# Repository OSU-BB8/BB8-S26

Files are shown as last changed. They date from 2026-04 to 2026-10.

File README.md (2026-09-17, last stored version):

# Picar-X

Picar-X Python library for Raspberry Pi.

## Links

- Docs: <https://docs.sunfounder.com/projects/picar-x-v20/en/latest/>
- Robot Hat: <https://docs.sunfounder.com/projects/robot-hat-v4/en/latest/>
- Forum: <https://forum.sunfounder.com/>
- Sunfounder: <https://www.sunfounder.com/>

## Installation

 > **Note**
  You also need to install robot_hat, vilib, sunfounder_controller and other dependent libraries.\
  <https://docs.sunfounder.com/projects/picar-x-v20/en/latest/python/python_start/install_all_modules.html>

```bash
# Install robot_hat
git clone --depth 1 -b 2.5.x https://github.com/sunfounder/robot-hat.git
cd robot-hat
sudo python3 install.py

# Install vilib
git clone --depth 1 https://github.com/sunfounder/vilib.git
cd vilib
sudo python3 install.py

# Install picar-x
git clone -b 2.1.x https://github.com/sunfounder/picar-x.git
cd picar-x
sudo pip3 install . --break
```

## Debug

Debug command records

```bash
cd ~/picar-x && sudo pip3 install . --break --no-deps --no-build-isolation
```

## Debug records

```bash
sudo pip3 uninstall picar-x --break -y && cd ~/picar-x && sudo pip3 install . --break --no-deps --no-build-isolation
sudo pip3 uninstall robot_hat --break -y && cd ~/robot-hat && sudo pip3 install . --break --no-deps --no-build-isolation
sudo python3 ~/picar-x/examples/14_voice_active_car_gpt.py
```

----------------------------------------------

## About SunFounder

SunFounder is a technology company focused on Raspberry Pi and Arduino open source community development. Committed to the promotion of open source culture, we strives to bring the fun of electronics making to people all around the world and enable everyone to be a maker. Our products include learning kits, development boards, robots, sensor modules and development tools. In addition to high quality products, SunFounder also offers video tutorials to help you make your own project. If you have interest in open source or making something cool, welcome to join us!

----------------------------------------------

## License

This program is free software; you can redistribute it and/or modify it under the terms of the GNU General Public License as published by the Free Software Foundation; either version 2 of the License, or (at your option) any later version.

This program is distributed in the hope that it will be useful, but WITHOUT ANY WARRANTY; without even the implied wa rranty of MERCHANTABILITY or FITNESS FOR A PARTICULAR PURPOSE. See the GNU General Public License for more details.

You should have received a copy of the GNU General Public License along with this program; if not, write to the Free Software Foundation, Inc., 51 Franklin Street, Fifth Floor, Boston, MA 02110-1301 USA.

{Repository Name} comes with ABSOLUTELY NO WARRANTY; for details run ./show w. This is free software, and you are welcome to redistribute it under certain conditions; run ./show c for details.

SunFounder, Inc., hereby disclaims all copyright interest in the program '{Repository Name}' (which makes passes at compilers).

Mike Huang, 21 August 2015

Mike Huang, Chief Executive Officer

Email: service@sunfounder.com, support@sunfounder.com

----------------------------------------------

## Contact us

website:
    www.sunfounder.com

E-mail:
    service@sunfounder.com, support@sunfounder.com

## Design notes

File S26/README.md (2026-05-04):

# BB8-S26
Welcome to the BB8 project! This repo has all the files that we used to develop the BB8 as well as a ton of old files from previous groups.

To test out the project, a few things need to be done first.

1. Plug the Pi on the main BB8 (Not the test one in the chassis) to a power source
2. You will need to connect the Pi to a monitor to find out its IP address and connect it to eduroam or whichever network you want to use.
3. The robot has two modes right now: The PS5 controller mode and the head-body communication mode that reads april tags.

PS5 Controller Mode:
1. Pair the PS5 controller with the body Pi (The one in the sphere). You can do this from the terminal or GUI
2. Plug in the 24V LiPo battery to the robot. This connects to everything except the Pi (which is a Pi 4B - definitely could use the upgrade to a 5, which should be in the materials).
3. Plug in the 3.7V with boost converter into the Pi and disconnect anything external from it.
4. Connect the shell so that it encapsulates the entire robot.
5. SSH into the body Pi. The user is "bb8" and password is "password" (I know right).
6. Navigate to /'BB8 Files'/'Body Files' 
7. Run the python files "PS5_Controller.py"
8. This will give you a menu of options to select. The two main ones are options 5 and 6. Choose 5 if you want the option that will balance the head and balance the body (Although the pendulum body balancer doesn't work well since the PID values are 0 for now). Option 6 gives the user full control over all the motors and functions.

Head-Body Communication:
1.You'll want to power up the head's Pi. This can be found on the picar, which we used for testing and then placed inside the head for Demo purposes.
2. Plug in the Head's Pi and navigate to the terminal. Form here, you should look at the terminal and find out the IP address.
3. Instead of pairing the PS5 Controller, go to the file "Expo_Demo.py" in 'BB8 Files'/'Expo Demo'. Replace the IP address in it with the new body IP address.
4. Make sure both the Body and the Head Pi's are turned on. 
5. Run Body_communication.py ON THE BODY. This opens up a UDP socket and waits for commands from the head.
6. Run Head_Communication.py ON THE HEAD. This allows you to send commands from the head to the body.
7. If you want to SSH into the head Pi, the user is "bb8camera" and the password is "password".

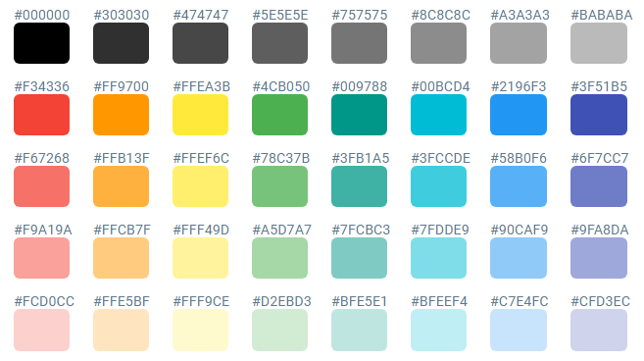
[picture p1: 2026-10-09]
F26/Head Code/April_Tag/docs/assets/media/colorboard_palette.png

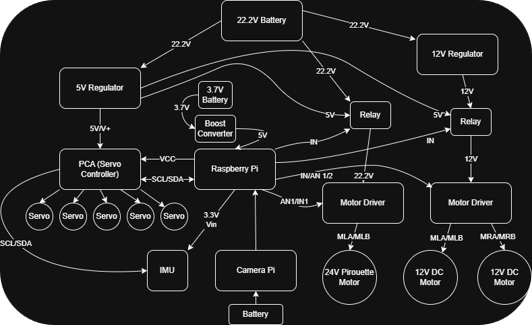
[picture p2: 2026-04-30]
S26/Electrical Flowchart.png

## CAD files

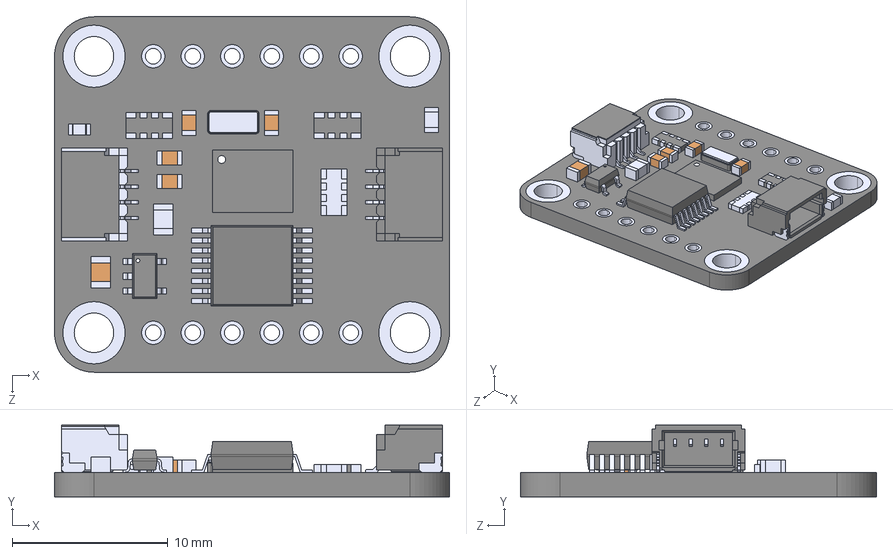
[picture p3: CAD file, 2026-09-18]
F26/PCB/Symbols & Footprints/BNO085/BNO085.step
25.4 x 4.60 x 22.9 mm
SPX5205M5
MAX4661CAE+

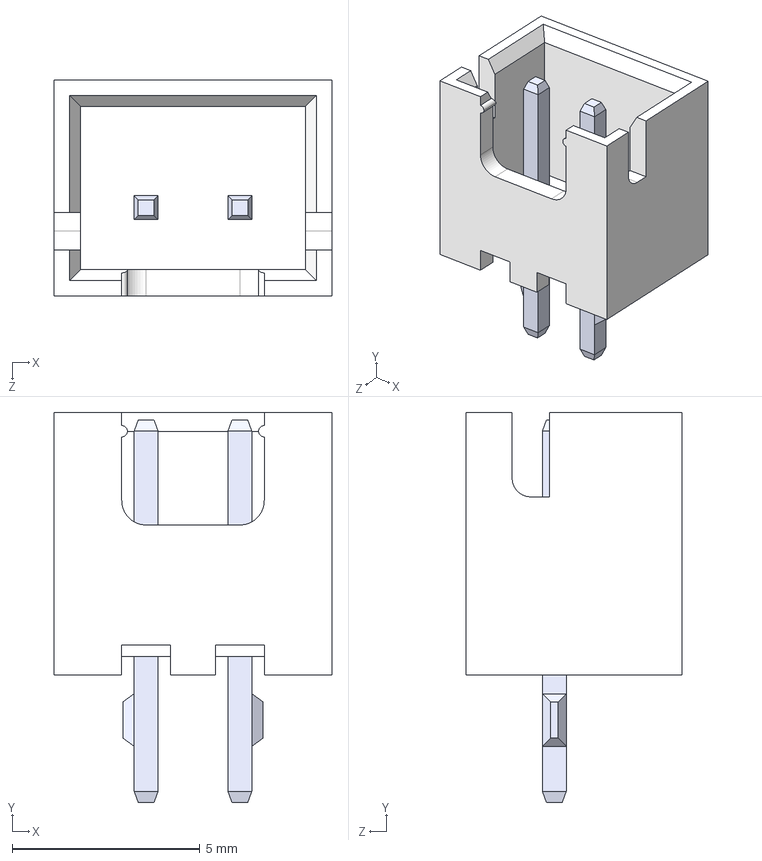
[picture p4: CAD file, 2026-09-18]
F26/PCB/Symbols & Footprints/JST/JST.step
7.40 x 10.4 x 5.75 mm

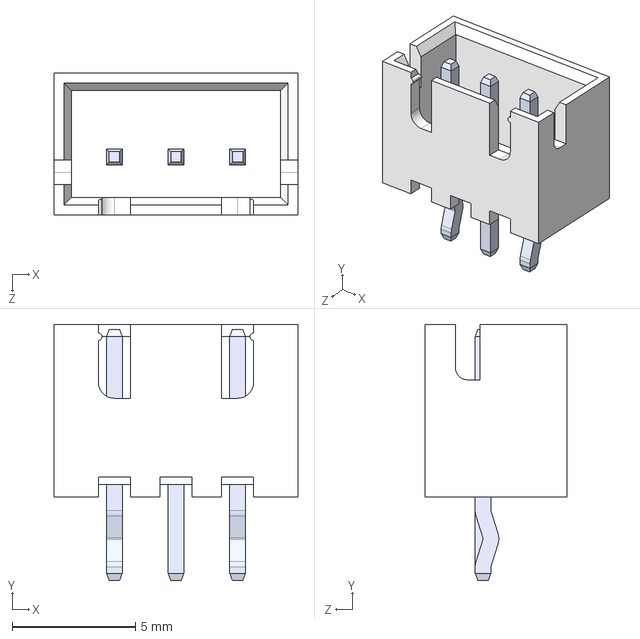
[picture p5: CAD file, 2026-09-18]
F26/PCB/Symbols & Footprints/JST3/JST3.step
9.90 x 10.4 x 5.75 mm

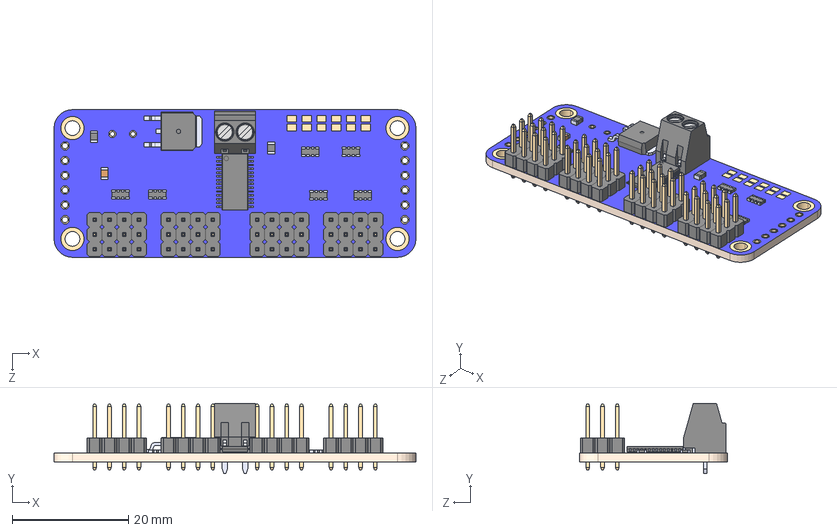
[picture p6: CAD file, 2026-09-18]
F26/PCB/Symbols & Footprints/PCA9685/PCA9685.step
62.2 x 12.1 x 25.4 mm
AOD417
TERMBLOCK_1X2-3.5MM
PCA9685_PCA9685
RESPACK_4X0603_220_ x 6

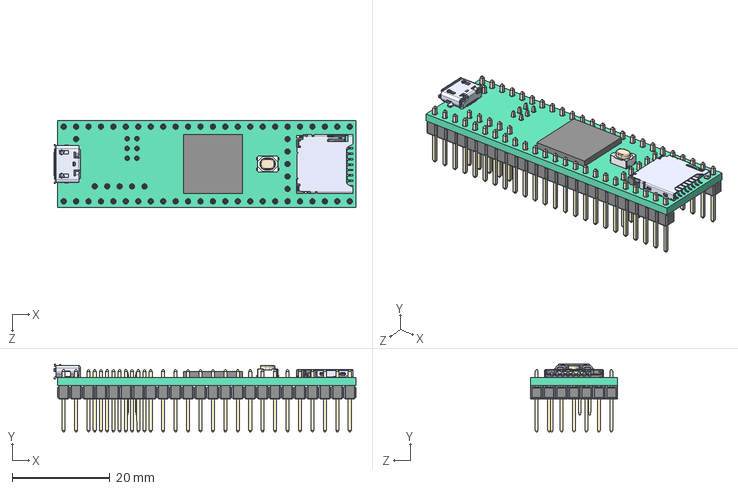
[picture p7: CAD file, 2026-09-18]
F26/PCB/Symbols & Footprints/Teensy/Teensy.step
61.7 x 13.8 x 17.8 mm

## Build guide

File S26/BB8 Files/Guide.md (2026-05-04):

Guide to the Files in this Directory:

1. Archive: Contains all the old, obsolete code for the project. Some are python files we developed, and others are C files for the Arduino from further back.

2. Body Files: Contains all the files to be used by the Body Pi.

3. Camera Files: Contains all the files to be used by the Head Pi.

4. Demo Videos: Contains videos that we got from demonstrations.

5. Expo Demo: Contains code that was used by the Head Pi for demonstrations.

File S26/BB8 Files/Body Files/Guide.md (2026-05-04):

Guide to the Files in this Directory:

1. Body_Communication: This is the file that receives commands from the head. If you want to run any APRILTag stuff, run the Body_Communication file on the Body Pi first.

2. Dead_Reckoning: This file allows the robot to locate how far it traveled from where it started. Currently, it doesn't work very well and isn't integrated into the system as a result. 

3. IMU: This file read the IMU data and sends it off the the Body via I2C.

4. Movement_Functions: This file contains all the movement functions and maps them to various motors or servos. If you want to control the robot, you must use a function from this file.

5. PID: This function has a basic PID class in it. The Movement_Functions uses it in its update_balance function.

6. PS5_Controller: This file allows a user to control the BB8 using a PS5 controller. To use it, simply make sure the Pi reads and is paired to your PS5 controller and run this code. When prompted, selected either option 5 or 6.

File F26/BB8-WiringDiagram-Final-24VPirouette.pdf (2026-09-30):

Vin 3Vo GND SDA SCL RST PS0 PS1 INT ADRBNO055 IMU

# PCA9685 GNDOE SCL SDA VCCV+ GND OESCL SDA VCC V+

## SmartDriveDuo-30

MLB
MLA
VB-VB+
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
AN2 ⁰ ¹ ² ³ ⁴ ⁵ ⁶ ⁷ ⁸ ⁹ ¹⁰ ¹¹ ¹² ¹³ ¹⁴ ¹⁵ PWM V+ GND 3V3 GPIO ² GPIO ³ GPIO ⁴ GND GPIO ¹⁷ GPIO ²⁷ GPIO ²² 3v3 GPIO ¹⁰ GPIO ⁹ GPIO ¹¹ GND GPIO ⁰ GPIO ⁵ GPIO ⁶ GPIO ¹³ GPIO ¹⁹ GPIO ²⁶ GND ⁵V5V GND GPIO ¹⁴ GPIO ¹⁵ GPIO ¹⁸ GND GPIO ²³ GPIO ²⁴ GND GPIO ²⁵ GPIO ⁸ GPIO ⁷ GPIO ¹ GND GPIO ¹² GND GPIO ¹⁶ GPIO ²⁰ GPIO ²¹ Raspberry Pi

4-Wire Connector
(Make Sure to line up)

## SmartDriveDuo-30

MLB
MLA
VB-VB+
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
4-Wire Connector
(Make Sure to line up)

## Drive Motor (Left)

## 22.2V LiPo Battery

2-Wire Connection
(Auto Lines up)

1 2 3 4 5 6

## Chunzehui F-1011

## Castle CC-BEC Pro

(5V)

Circle Thingy
(Wires Wrapped Around)

## Drive Motor (Right)

Red

Black | 2 Red

# 2 Black 1 Red ⁽Power) 1 Black ⁽GND⁾

## Swing Pendulum Servo (Front)

White Wire

Red Wire

Black Wire

## Swing Pendulum Servo (Back)

### 3 Wires

Basically
Together

Head Servo
(Move Left & Right)

Head Servo
(Move Forward
& Backward)

Head
Spinning
Servo

Yellow
Brown

Red

12V
Pirouette Motor
(Bottom)

## Castle CC-BEC Pro

(12V) Circle Thingy
(Wires
Wrapped
Around)

V+

GND

GND Wire

## 5V Signal Relay

(12V)

IN
GND
PWR

NC
NO
COM

## 5V Signal Relay

(24V)

IN
GND
PWR

NC
NO
COM

--- C:\Users\sawhu\OneDrive - Oklahoma A and M System\Documents\LTspice\BB8 - Final Wiring Diagram (24V Motor).asc ---

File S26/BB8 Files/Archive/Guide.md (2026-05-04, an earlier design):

Guide to the Files in this directory:

1. Body/Old Code: Contains Arduino code that old groups used.

2. Continuous Spin Tests: Old code to test the motors. Probably not working anymore due to the changes we made.

3. Dome: Old Arduino code for the head system.

4. Remote: Old code to control BB8 using a phone.

5. Scampa123s BB8 Code: More old code written for Arduino.

6. Test Files: Old files that we developed in Python. Might be worth looking at if needing some ideas or wanting to figure out how system works.

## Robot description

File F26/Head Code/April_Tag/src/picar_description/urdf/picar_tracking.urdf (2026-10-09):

<?xml version="1.0"?>
<!--
  picar_tracking.urdf  (V3)
  URDF for live RViz visualization.  Root frame is 'car_base', published by
  tf_bridge as 'world -> car_base'.  Pan and tilt are revolute joints; their
  positions come from /joint_states published by tf_bridge each frame.

  Coordinate convention (all frames, including car_base):
    +X = image right
    +Y = image down  (OpenCV / pupil-apriltags camera convention)
    +Z = optical axis (forward, toward tags)

  Physical kinematic chain (parent -> child):
    car_base (chassis level)
      -> pan_joint  (revolute, Y-axis, yaw / pan)    height ~6 cm above chassis
      -> tilt_joint (revolute, X-axis, pitch / tilt)  height ~2 cm above pan
      -> camera     (fixed, camera optical frame)      height ~1.5 cm above tilt

  Joint offsets are approximate.  Each is marked with TUNE and should be
  verified against physical measurements and/or compared with RViz after a
  live-pan test (car_base world position should remain stable as servos move).
-->
<robot name="picar_tracking">

  <material name="picar_white">
    <color rgba="0.9 0.9 0.9 1.0"/>
  </material>
  <material name="picar_black">
    <color rgba="0.1 0.1 0.1 1.0"/>
  </material>
  <material name="picar_gray">
    <color rgba="0.5 0.5 0.5 1.0"/>
  </material>
  <material name="picar_blue">
    <color rgba="0.2 0.4 0.85 0.85"/>
  </material>

  <!-- ROOT: car body frame — published by tf_bridge as 'world -> car_base'. -->
  <!-- No visual here; chassis box is a separate child link.                 -->
  <link name="car_base"/>

  <!-- Pan servo link — visualised as a small horizontal cylinder -->
  <link name="pan_link">
    <visual>
      <origin xyz="0 0 0" rpy="1.5708 0 0"/>
      <geometry>
        <cylinder length="0.05" radius="0.008"/>
      </geometry>
      <material name="picar_gray"/>
    </visual>
  </link>
  <!--
    TUNE: pan servo is approximately 6 cm above car_base (-Y = up in camera
    convention).  Adjust xyz y-value after visual inspection in RViz.
  -->
  <joint name="pan_joint" type="revolute">
    <parent link="car_base"/>
    <child link="pan_link"/>
    <origin xyz="0.0 -0.060 0.0" rpy="0 0 0"/>
    <axis xyz="0 1 0"/>
    <limit lower="-1.5708" upper="1.5708" effort="1.0" velocity="1.0"/>
  </joint>

  <!-- Tilt servo link — visualised as a small vertical cylinder -->
  <link name="tilt_link">
    <visual>
      <origin xyz="0 0 0" rpy="0 0 0"/>
      <geometry>
        <cylinder length="0.03" radius="0.008"/>
      </geometry>
      <material name="picar_gray"/>
    </visual>
  </link>
  <!-- TUNE: tilt servo is approximately 2 cm above pan_link. -->
  <joint name="tilt_joint" type="revolute">
    <parent link="pan_link"/>
    <child link="tilt_link"/>
    <origin xyz="0.0 -0.020 0.0" rpy="0 0 0"/>
    <axis xyz="1 0 0"/>
    <limit lower="-0.6109" upper="0.6109" effort="1.0" velocity="1.0"/>
  </joint>

  <!-- Camera optical frame — matches tf_bridge 'camera' TF convention.      -->
  <!-- Small blue box at the camera lens position.                            -->
  <link name="camera">
    <visual>
      <origin xyz="0 0 0" rpy="0 0 0"/>
      <geometry>
        <box size="0.025 0.025 0.02"/>
      </geometry>
      <material name="picar_blue"/>
    </visual>
  </link>
  <!-- TUNE: camera lens is approximately 1.5 cm above tilt_link. -->
  <joint name="camera_optical_joint" type="fixed">
    <parent link="tilt_link"/>
    <child link="camera"/>
    <origin xyz="0.0 -0.015 0.0" rpy="0 0 0"/>
  </joint>

  <!-- Camera pan/tilt mount column — purely visual, child of camera. -->
  <link name="camera_mount">
    <visual>
      <origin xyz="0 0 0" rpy="0 0 0"/>
      <geometry>
        <box size="0.03 0.07 0.03"/>
      </geometry>
      <material name="picar_gray"/>
    </visual>
  </link>
  <joint name="camera_to_mount" type="fixed">
    <parent link="camera"/>
    <child link="camera_mount"/>
    <!-- column is below (+Y=down) and slightly behind (-Z) the camera lens -->
    <origin xyz="0.0 0.045 -0.01" rpy="0 0 0"/>
  </joint>

  <!-- Car chassis — 14 cm wide, 4 cm tall, 20 cm long (camera convention). -->
  <link name="base_link">
    <visual>
      <origin xyz="0 0 0" rpy="0 0 0"/>
      <geometry>
        <box size="0.14 0.04 0.20"/>
      </geometry>
      <material name="picar_white"/>
    </visual>
  </link>
  <!--
    TUNE: chassis centre is 5 cm behind car_base along the optical axis (-Z
    offset).  The Y offset keeps chassis box at approximately car_base height
    (no vertical offset since car_base is defined at chassis-top level).
    Adjust after visual inspection in RViz.
  -->
  <joint name="car_base_to_chassis" type="fixed">
    <parent link="car_base"/>
    <child link="base_link"/>
    <origin xyz="0.0 0.0 -0.05" rpy="0 0 0"/>
  </joint>

  <!-- Front left wheel -->
  <link name="front_left_wheel">
    <visual>
      <origin xyz="0 0 0" rpy="0 1.5708 0"/>
      <geometry>
        <cylinder length="0.03" radius="0.033"/>
      </geometry>
      <material name="picar_black"/>
    </visual>
  </link>
  <joint name="chassis_to_fl_wheel" type="fixed">
    <parent link="base_link"/>
    <child link="front_left_wheel"/>
    <origin xyz="-0.07 0.02 0.07" rpy="0 0 0"/>
  </joint>

  <!-- Front right wheel -->
  <link name="front_right_wheel">
    <visual>
      <origin xyz="0 0 0" rpy="0 1.5708 0"/>
      <geometry>
        <cylinder length="0.03" radius="0.033"/>
      </geometry>
      <material name="picar_black"/>
    </visual>
  </link>
  <joint name="chassis_to_fr_wheel" type="fixed">
    <parent link="base_link"/>
    <child link="front_right_wheel"/>
    <origin xyz="0.07 0.02 0.07" rpy="0 0 0"/>
  </joint>

  <!-- Rear left wheel -->
  <link name="rear_left_wheel">
    <visual>
      <origin xyz="0 0 0" rpy="0 1.5708 0"/>
      <geometry>
        <cylinder length="0.03" radius="0.033"/>
      </geometry>
      <material name="picar_black"/>
    </visual>
  </link>
  <joint name="chassis_to_rl_wheel" type="fixed">
    <parent link="base_link"/>
    <child link="rear_left_wheel"/>
    <origin xyz="-0.07 0.02 -0.07" rpy="0 0 0"/>
  </joint>

  <!-- Rear right wheel -->
  <link name="rear_right_wheel">
    <visual>
      <origin xyz="0 0 0" rpy="0 1.5708 0"/>
      <geometry>
        <cylinder length="0.03" radius="0.033"/>
      </geometry>
      <material name="picar_black"/>
    </visual>
  </link>
  <joint name="chassis_to_rr_wheel" type="fixed">
    <parent link="base_link"/>
    <child link="rear_right_wheel"/>
    <origin xyz="0.07 0.02 -0.07" rpy="0 0 0"/>
  </joint>

</robot>

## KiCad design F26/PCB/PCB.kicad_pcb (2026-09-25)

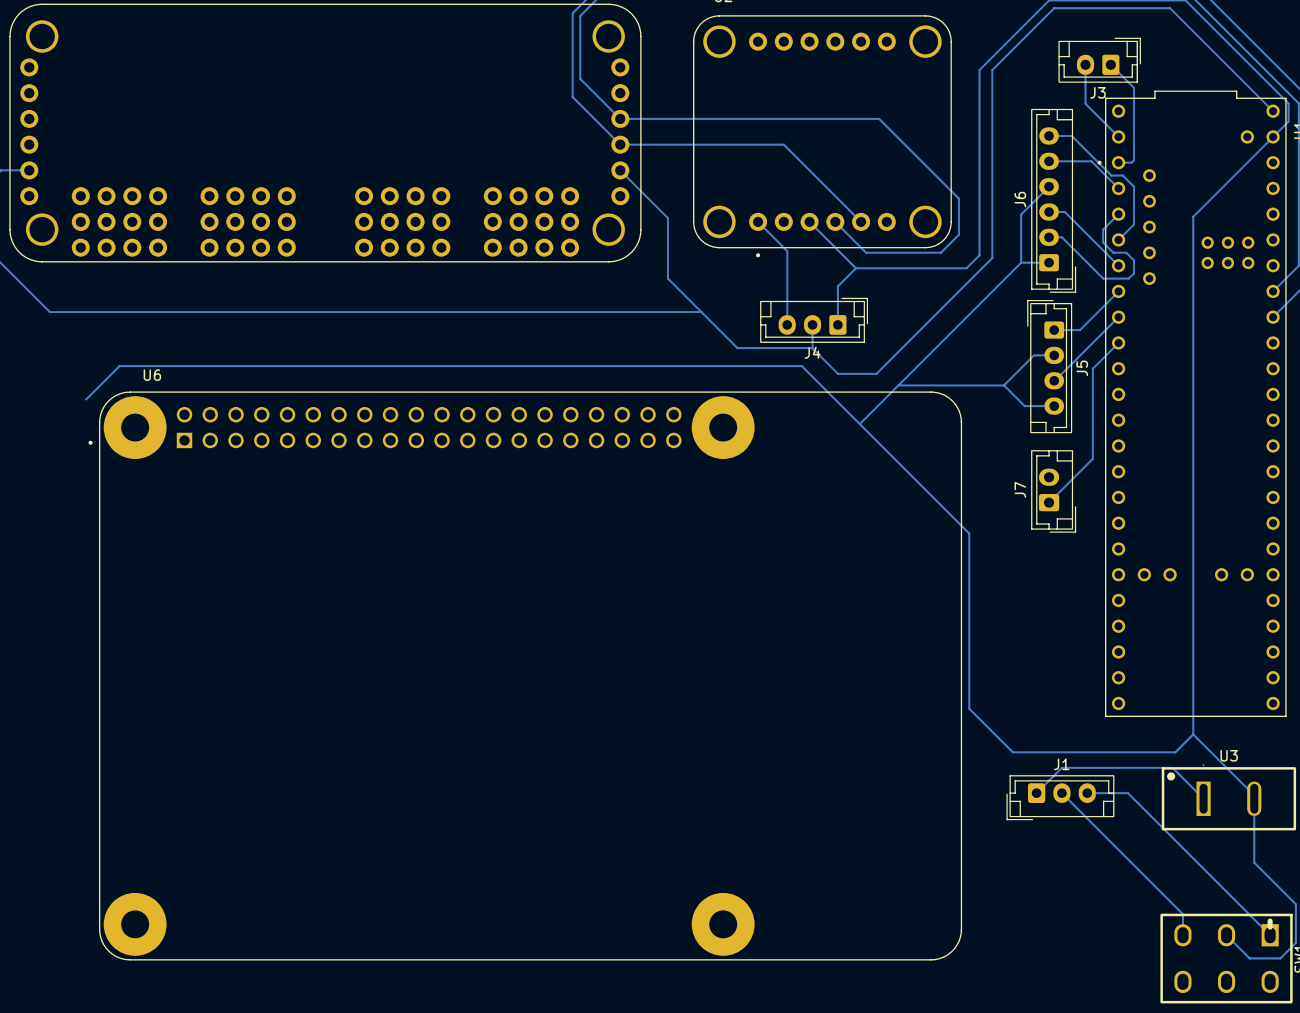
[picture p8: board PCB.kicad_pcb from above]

Board: 2 copper layers, 12 parts (0 on the bottom side), 23 nets.

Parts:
J1, J4: B3B-XH-A; JST_EH_B3B-EH-A_1x03_P2.50mm_Vertical
J3: B2B-XH-A; JST_EH_B2B-EH-A_1x02_P2.50mm_Vertical
J5: Conn_01x04; JST_EH_B4B-EH-A_1x04_P2.50mm_Vertical
J6: Conn_01x06; JST_EH_B6B-EH-A_1x06_P2.50mm_Vertical
J7: Conn_01x02; JST_EH_B2B-EH-A_1x02_P2.50mm_Vertical
SW1: SW_Nidec_CAS-120A1; Mini_Toggle_DPDT_4.3x4.6mm
U1: Teensy
U2: MODULE_BNO085
U3: Switch_2Pin_5mm_ParallelBlades
U4: 815; MODULE_PCA9685
U6: SC0194_9_; MODULE_SC0194_9_

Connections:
3V3: U6.1 (3V3), U6.17 (3V3)
5V0: U6.2 (5V0), U6.4 (5V0)
GND: U4.GND_1 (GND), U4.GND_2 (GND), U4.GND_3 (GND), U4.GND_4 (GND), U4.GND_5 (GND), U4.GND_6 (GND), U4.GND_7 (GND), U4.GND_8 (GND), U4.GND_9 (GND), U4.GND_10 (GND), U4.GND_11 (GND), U4.GND_12 (GND), U4.GND_13 (GND), U4.GND_14 (GND), U4.GND_15 (GND), U4.GND_16 (GND), U4.GND_17 (GND), U4.GND_18 (GND), U6.6 (GND), U6.9 (GND), U6.14 (GND), U6.20 (GND), U6.25 (GND), U6.30 (GND), U6.34 (GND), U6.39 (GND)
unnamed: J1.1, U3.1
unnamed: J5.1, U1.6 (OUT1D)
unnamed: J4.1, J5.2, J5.4, J6.1, J6.4, SW1.2 (B), U1.GND, U2.3 (GND), U3.2
unnamed: J5.3, U1.7 (OUT1A)
unnamed: J6.2, U1.3 (LRCLK2)
unnamed: J6.3, U1.5 (IN2)
unnamed: J6.5, U1.2 (OUT2)
unnamed: J6.6, U1.4 (BCLK2)
unnamed: J7.1 (Pin_1_1), U1.8 (IN1)
unnamed: J1.2, SW1.3 (A)
unnamed: J1.3, SW1.1 (C)
unnamed: U1.18 (A4), U2.5 (SDA), U4.SDA_1 (SDA), U4.SDA_2 (SDA)
unnamed: U1.19 (A5), U2.4 (SCL), U4.SCL_1 (SCL), U4.SCL_2 (SCL)
unnamed: J3.2, U1.0 (RX1)
unnamed: J3.1, U1.1 (TX1)
unnamed: J4.3, U2.1 (VIN)
unnamed: U4.OE_1 (~OE), U4.OE_2 (~OE)
SHIELD: U6.S1 (SHIELD), U6.S2 (SHIELD), U6.S3 (SHIELD), U6.S4 (SHIELD)
V+: U4.V+_1 (V+), U4.V+_2 (V+), U4.V+_3 (V+), U4.V+_4 (V+), U4.V+_5 (V+), U4.V+_6 (V+), U4.V+_7 (V+), U4.V+_8 (V+), U4.V+_9 (V+), U4.V+_10 (V+), U4.V+_11 (V+), U4.V+_12 (V+), U4.V+_13 (V+), U4.V+_14 (V+), U4.V+_15 (V+), U4.V+_16 (V+), U4.V+_17 (V+), U4.V+_18 (V+)
VCC: J4.2, U1.Vin, U4.VCC_1 (VCC), U4.VCC_2 (VCC)

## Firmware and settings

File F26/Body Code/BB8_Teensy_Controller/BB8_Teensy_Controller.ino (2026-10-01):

/*
  BB-8 Teensy 4.1 Motor / Navigation Controller

  Pi sends:
      T,<distance_ft>,<angle_deg>\n
  Example:
      T,15.7,-32.5

  Teensy replies periodically:
      S,<state>,<distance>,<angle>,<pitch>,<roll>,<drive>,<swing>,<pivot>

  IMPORTANT:
  - Verify all Teensy pin assignments below before connecting motor drivers.
  - Teensy 4.1 GPIO is 3.3 V logic.
  - Pi and Teensy MUST share GND.
  - Motor power must NOT come from the Teensy.
*/

#include <Arduino.h>
#include <Wire.h>
#include <Adafruit_PWMServoDriver.h>
#include <Adafruit_BNO08x.h>

// ============================================================
// PIN ASSIGNMENTS - CHANGE TO MATCH NEW WIRING
// ============================================================

// Pi UART: Teensy Serial1 RX=0, TX=1
constexpr uint8_t DRIVE1_PHASE_PIN  = 2;
constexpr uint8_t DRIVE1_PWM_PIN    = 3;
constexpr uint8_t DRIVE2_PHASE_PIN  = 4;
constexpr uint8_t DRIVE2_PWM_PIN    = 5;
constexpr uint8_t PIVOT_PHASE_PIN   = 6;
constexpr uint8_t PIVOT_PWM_PIN     = 7;

constexpr uint8_t RELAY1_PIN = 8;

// PCA9685
constexpr uint8_t PCA_ADDRESS = 0x40;
constexpr uint8_t SWING1_CH = 0;
constexpr uint8_t SWING2_CH = 4;

// Head servos (same PCA9685 channels as the original Pi controller)
constexpr uint8_t HEAD_FB_CH  = 1;  // head forward/back
constexpr uint8_t HEAD_STS_CH = 2;  // head side-to-side

// ============================================================
// CONFIGURATION
// ============================================================

constexpr uint32_t PI_BAUD = 115200;
constexpr uint32_t USB_BAUD = 115200;

constexpr float FOLLOW_START_DISTANCE_FT = 5.0f;
constexpr float FOLLOW_STOP_DISTANCE_FT  = 4.0f;
constexpr float HARD_MIN_DISTANCE_FT     = 3.0f;
constexpr float MAX_VALID_DISTANCE_FT    = 40.0f;

constexpr float MAX_DRIVE_SPEED = 0.30f;
constexpr float MIN_DRIVE_SPEED = 0.12f;
constexpr float FULL_SPEED_DISTANCE_FT = 18.0f;
constexpr float DRIVE_ACCEL_RATE = 0.40f;
constexpr float DRIVE_DECEL_RATE = 0.70f;

constexpr float ANGLE_DEADBAND_DEG = 6.0f;
constexpr float CLOSE_PIVOT_START_ANGLE_DEG = 30.0f;
constexpr float PIVOT_STOP_ANGLE_DEG = 10.0f;
constexpr float REAR_PIVOT_ANGLE_DEG = 65.0f;
constexpr float CLOSE_NAV_DISTANCE_FT = 10.0f;

constexpr float SWING_CENTER_DEG = 90.0f;
constexpr float MAX_SWING_OFFSET_DEG = 14.0f;
constexpr float SWING_KP = 0.35f;
constexpr float SWING_DIRECTION = 1.0f;
constexpr float MIN_SWING_OFFSET_DEG = 1.5f;
constexpr float SWING_SLEW_RATE_DEG_PER_SEC = 35.0f;

constexpr float PIVOT_KP = 0.022f;
constexpr float MIN_PIVOT_COMMAND = 0.10f;
constexpr float MAX_PIVOT_COMMAND = 0.25f;
constexpr float PIVOT_DIRECTION = -1.0f;

constexpr float DISTANCE_FILTER_ALPHA = 0.25f;
constexpr float ANGLE_FILTER_ALPHA = 0.30f;

constexpr uint32_t PI_TIMEOUT_MS = 500;
constexpr uint32_t CONTROL_PERIOD_US = 20000; // 50 Hz
constexpr uint32_t STATUS_PERIOD_MS = 250;

// Servo calibration.
// Tune these to your actual servos if necessary.
constexpr uint16_t SERVO_MIN_US = 500;
constexpr uint16_t SERVO_MAX_US = 2500;

// Head leveling configuration.
// Original Pi behavior was FB = 90 + pitch and STS = 90 + roll.
constexpr float HEAD_CENTER_DEG = 90.0f;
constexpr float HEAD_MIN_DEG = 55.0f;
constexpr float HEAD_MAX_DEG = 125.0f;
constexpr float HEAD_FB_OFFSET_DEG = 2.5f;
constexpr float HEAD_STS_OFFSET_DEG = -2.0f;
constexpr float HEAD_EMA_ALPHA = 0.15f;
constexpr float HEAD_PITCH_DIRECTION = 1.0f;
constexpr float HEAD_ROLL_DIRECTION  = 1.0f;

// ============================================================
// HARDWARE OBJECTS
// ============================================================

Adafruit_PWMServoDriver pca(PCA_ADDRESS);
Adafruit_BNO08x bno08x(-1);
sh2_SensorValue_t sensorValue;

bool imuOK = false;
float imuPitch = 0.0f;
float imuRoll = 0.0f;
float imuYaw = 0.0f;

// Smoothed head commands.
float headFBCommand = HEAD_CENTER_DEG;
float headSTSCommand = HEAD_CENTER_DEG;
bool headFilterInitialized = false;

// ============================================================
// CONTROLLER STATE
// ============================================================

enum NavState {
  STARTUP,
  WAITING_FOR_PI,
  IN_LEASH_ZONE,
  TARGET_REACHED,
  TOO_CLOSE,
  STRAIGHT,
  ARC,
  PIVOT,
  INVALID_TARGET,
  COMMS_LOST
};

NavState navState = STARTUP;

bool following = false;
bool pivoting = false;
bool systemEnabled = false;

bool haveFilteredTarget = false;
float filteredDistance = 0.0f;
float filteredAngle = 0.0f;

float currentDrive = 0.0f;
float currentSwing = SWING_CENTER_DEG;
float currentPivot = 0.0f;

uint32_t lastPacketMs = 0;
uint32_t lastControlUs = 0;
uint32_t lastStatusMs = 0;

char rxBuffer[80];
size_t rxIndex = 0;

// ============================================================
// HELPERS
// ============================================================

float clampf(float x, float lo, float hi) {
  if (x < lo) return lo;
  if (x > hi) return hi;
  return x;
}

float moveToward(float current, float target, float maxChange) {
  if (target > current) return min(current + maxChange, target);
  if (target < current) return max(current - maxChange, target);
  return current;
}

float normalizeAngle(float a) {
  while (a > 180.0f) a -= 360.0f;
  while (a < -180.0f) a += 360.0f;
  return a;
}

const char* stateName(NavState s) {
  switch (s) {
    case STARTUP: return "STARTUP";
    case WAITING_FOR_PI: return "WAIT_PI";
    case IN_LEASH_ZONE: return "LEASH";
    case TARGET_REACHED: return "REACHED";
    case TOO_CLOSE: return "TOO_CLOSE";
    case STRAIGHT: return "STRAIGHT";
    case ARC: return "ARC";
    case PIVOT: return "PIVOT";
    case INVALID_TARGET: return "INVALID";
    case COMMS_LOST: return "COMMS_LOST";
    default: return "UNKNOWN";
  }
}

// ============================================================
// MOTOR OUTPUT
// Phase/Enable behavior equivalent to gpiozero PhaseEnableMotor.
// ============================================================

void setPhaseEnableMotor(uint8_t phasePin, uint8_t pwmPin, float command) {
  command = clampf(command, -1.0f, 1.0f);

  if (fabsf(command) < 0.001f) {
    analogWrite(pwmPin, 0);
    digitalWrite(phasePin, LOW);
    return;
  }

  bool direction = command >= 0.0f;
  digitalWrite(phasePin, direction ? HIGH : LOW);

  int pwm = (int)roundf(fabsf(command) * 255.0f);
  pwm = constrain(pwm, 0, 255);
  analogWrite(pwmPin, pwm);
}

void drive(float command) {
  command = clampf(command, -MAX_DRIVE_SPEED, MAX_DRIVE_SPEED);
  setPhaseEnableMotor(DRIVE1_PHASE_PIN, DRIVE1_PWM_PIN, -command);
  setPhaseEnableMotor(DRIVE2_PHASE_PIN, DRIVE2_PWM_PIN, -command);
}

void steer(float command) {
  command = clampf(command, -1.0f, 1.0f);
  if (fabsf(command) < 0.01f) command = 0.0f;
  setPhaseEnableMotor(PIVOT_PHASE_PIN, PIVOT_PWM_PIN, command);
}

uint16_t servoPulseFromDegrees(float degrees) {
  degrees = clampf(degrees, 0.0f, 180.0f);
  float us = SERVO_MIN_US +
             (degrees / 180.0f) * (SERVO_MAX_US - SERVO_MIN_US);

  // PCA9685 at 50 Hz => 20,000 us period / 4096 counts.
  return (uint16_t)roundf(us * 4096.0f / 20000.0f);
}

void setServoDegrees(uint8_t channel, float degrees) {
  pca.setPWM(channel, 0, servoPulseFromDegrees(degrees));
}

void setHeadForwardBack(float degrees) {
  degrees = clampf(degrees, HEAD_MIN_DEG, HEAD_MAX_DEG);
  setServoDegrees(HEAD_FB_CH, degrees + HEAD_FB_OFFSET_DEG);
}

void setHeadSideToSide(float degrees) {
  degrees = clampf(degrees, HEAD_MIN_DEG, HEAD_MAX_DEG);
  setServoDegrees(HEAD_STS_CH, degrees + HEAD_STS_OFFSET_DEG);
}

void centerHead() {
  headFBCommand = HEAD_CENTER_DEG;
  headSTSCommand = HEAD_CENTER_DEG;
  headFilterInitialized = false;
  setHeadForwardBack(HEAD_CENTER_DEG);
  setHeadSideToSide(HEAD_CENTER_DEG);
}

void updateHeadLeveling() {
  if (!imuOK) return;

  // Match the original Raspberry Pi behavior:
  // forward/back follows pitch; side-to-side follows roll.
  float targetFB = HEAD_CENTER_DEG + HEAD_PITCH_DIRECTION * imuPitch;
  float targetSTS = HEAD_CENTER_DEG + HEAD_ROLL_DIRECTION * imuRoll;

  targetFB = clampf(targetFB, HEAD_MIN_DEG, HEAD_MAX_DEG);
  targetSTS = clampf(targetSTS, HEAD_MIN_DEG, HEAD_MAX_DEG);

  if (!headFilterInitialized) {
    headFBCommand = targetFB;
    headSTSCommand = targetSTS;
    headFilterInitialized = true;
  } else {
    headFBCommand += HEAD_EMA_ALPHA * (targetFB - headFBCommand);
    headSTSCommand += HEAD_EMA_ALPHA * (targetSTS - headSTSCommand);
  }

  setHeadForwardBack(headFBCommand);
  setHeadSideToSide(headSTSCommand);
}

void setSwing(float degrees) {
  // Preserve original Movement_Functions behavior:
  // difference = current_swing - 90 + swing_offset
  // servo1 = 90 + difference
  // servo2 = 90 - difference
  constexpr float swingOffset = -1.0f;

  degrees = clampf(degrees, 70.0f, 117.0f);
  float difference = degrees - 90.0f + swingOffset;

  setServoDegrees(SWING1_CH, 90.0f + difference);
  setServoDegrees(SWING2_CH, 90.0f - difference);
}

void enableSystem() {
  // Outputs are already zero before relays close.
  drive(0.0f);
  steer(0.0f);
  setSwing(90.0f);
  delay(20);

  digitalWrite(RELAY1_PIN, HIGH);
  systemEnabled = true;
}

void disableSystem() {
  drive(0.0f);
  steer(0.0f);
  setSwing(90.0f);

  digitalWrite(RELAY1_PIN, LOW);
  systemEnabled = false;
}

void emergencyStop(NavState reason) {
  currentDrive = 0.0f;
  currentPivot = 0.0f;
  currentSwing = SWING_CENTER_DEG;

  drive(0.0f);
  steer(0.0f);
  setSwing(SWING_CENTER_DEG);

  following = false;
  pivoting = false;
  navState = reason;
}

// ============================================================
// BNO085
// ============================================================

void setReports() {
  if (!imuOK) return;

  if (!bno08x.enableReport(SH2_ROTATION_VECTOR, 10000)) {
    Serial.println("WARNING: Could not enable BNO085 rotation vector");
  }
}

void quaternionToEuler(float qr, float qi, float qj, float qk,
                       float &yaw, float &pitch, float &roll) {
  float sqr = qr * qr;
  float sqi = qi * qi;
  float sqj = qj * qj;
  float sqk = qk * qk;

  yaw = atan2f(2.0f * (qi * qj + qk * qr),
               (sqi - sqj - sqk + sqr));

  float sinp = -2.0f * (qi * qk - qj * qr);
  sinp = clampf(sinp, -1.0f, 1.0f);
  pitch = asinf(sinp);

  roll = atan2f(2.0f * (qj * qk + qi * qr),
                (-sqi - sqj + sqk + sqr));

  constexpr float RAD_TO_DEG_F = 57.2957795f;
  yaw *= RAD_TO_DEG_F;
  pitch *= RAD_TO_DEG_F;
  roll *= RAD_TO_DEG_F;
}

void updateIMU() {
  if (!imuOK) return;

  if (bno08x.wasReset()) {
    setReports();
  }

  while (bno08x.getSensorEvent(&sensorValue)) {
    if (sensorValue.sensorId == SH2_ROTATION_VECTOR) {
      quaternionToEuler(
        sensorValue.un.rotationVector.real,
        sensorValue.un.rotationVector.i,
        sensorValue.un.rotationVector.j,
        sensorValue.un.rotationVector.k,
        imuYaw, imuPitch, imuRoll
      );
    }
  }
}

// ============================================================
// TARGET FILTER
// ============================================================

void resetTargetFilter() {
  haveFilteredTarget = false;
}

void filterTarget(float distance, float angle) {
  angle = normalizeAngle(angle);

  if (!haveFilteredTarget) {
    filteredDistance = distance;
    filteredAngle = angle;
    haveFilteredTarget = true;
    return;
  }

  filteredDistance =
      DISTANCE_FILTER_ALPHA * distance +
      (1.0f - DISTANCE_FILTER_ALPHA) * filteredDistance;

  float error = normalizeAngle(angle - filteredAngle);

  filteredAngle = normalizeAngle(
      filteredAngle + ANGLE_FILTER_ALPHA * error
  );
}

// ============================================================
// PI SERIAL PROTOCOL
// ============================================================

void handleCommand(char *line) {
  // Target packet: T,distance_ft,angle_deg
  if (line[0] == 'T' && line[1] == ',') {
    char *p1 = strchr(line + 2, ',');
    if (!p1) return;

    *p1 = '\0';

    float distance = atof(line + 2);
    float angle = atof(p1 + 1);

    if (!isfinite(distance) || !isfinite(angle) ||
        distance < 0.0f || distance > MAX_VALID_DISTANCE_FT) {
      emergencyStop(INVALID_TARGET);
      return;
    }

    filterTarget(distance, angle);
    lastPacketMs = millis();

    // Do not energize motor power until first valid command.
    if (!systemEnabled) enableSystem();

    return;
  }

  // Pause movement but KEEP motor power / relays enabled.
  if (strcmp(line, "PAUSE") == 0) {
      emergencyStop(WAITING_FOR_PI);

      // Throw away the old target so BB-8 cannot resume
      // toward stale beacon data.
      resetTargetFilter();

      // Keep the system enabled.
      // DO NOT call disableSystem().
      if (!systemEnabled) {
          enableSystem();
      }

      // PAUSE counts as valid Pi communication.
      lastPacketMs = millis();

      return;
  }

  // Explicit stop from Pi.
  if (strcmp(line, "STOP") == 0) {
    emergencyStop(WAITING_FOR_PI);
    disableSystem();
    resetTargetFilter();
    return;
  }

  // Optional heartbeat that does NOT command motion.
  if (strcmp(line, "PING") == 0) {
    Serial1.println("PONG");
    return;
  }
}

void readPiSerial() {
  while (Serial1.available()) {
    char c = (char)Serial1.read();

    if (c == '\r') continue;

    if (c == '\n') {
      rxBuffer[rxIndex] = '\0';
      if (rxIndex > 0) handleCommand(rxBuffer);
      rxIndex = 0;
      continue;
    }

    if (rxIndex < sizeof(rxBuffer) - 1) {
      rxBuffer[rxIndex++] = c;
    } else {
      // Overflow = discard packet safely.
      rxIndex = 0;
    }
  }
}

// ============================================================
// NAVIGATION
// ============================================================

float calculateDriveSpeed(float distance) {
  if (distance <= FOLLOW_STOP_DISTANCE_FT) return 0.0f;
  if (distance >= FULL_SPEED_DISTANCE_FT) return MAX_DRIVE_SPEED;

  float progress =
      (distance - FOLLOW_STOP_DISTANCE_FT) /
      (FULL_SPEED_DISTANCE_FT - FOLLOW_STOP_DISTANCE_FT);

  float speed =
      MIN_DRIVE_SPEED +
      progress * (MAX_DRIVE_SPEED - MIN_DRIVE_SPEED);

  return clampf(speed, MIN_DRIVE_SPEED, MAX_DRIVE_SPEED);
}

float calculateSwingTarget(float angle) {
  if (fabsf(angle) <= ANGLE_DEADBAND_DEG)
    return SWING_CENTER_DEG;

  float offset = angle * SWING_KP * SWING_DIRECTION;
  offset = clampf(offset, -MAX_SWING_OFFSET_DEG,
                  MAX_SWING_OFFSET_DEG);

  if (fabsf(offset) > 0.0f &&
      fabsf(offset) < MIN_SWING_OFFSET_DEG) {
    offset = copysignf(MIN_SWING_OFFSET_DEG, offset);
  }

  return SWING_CENTER_DEG + offset;
}

float calculatePivotCommand(float angle) {
  if (fabsf(angle) <= PIVOT_STOP_ANGLE_DEG)
    return 0.0f;

  float command = angle * PIVOT_KP * PIVOT_DIRECTION;

  if (fabsf(command) > 0.0f &&
      fabsf(command) < MIN_PIVOT_COMMAND) {
    command = copysignf(MIN_PIVOT_COMMAND, command);
  }

  return clampf(command, -MAX_PIVOT_COMMAND,
                MAX_PIVOT_COMMAND);
}

void commandDrive(float target, float dt) {
  target = clampf(target, -MAX_DRIVE_SPEED, MAX_DRIVE_SPEED);

  float rate =
      fabsf(target) > fabsf(currentDrive)
      ? DRIVE_ACCEL_RATE
      : DRIVE_DECEL_RATE;

  currentDrive = moveToward(
      currentDrive, target, rate * dt
  );

  drive(currentDrive);
}

void commandSwing(float target, float dt) {
  target = clampf(
      target,
      SWING_CENTER_DEG - MAX_SWING_OFFSET_DEG,
      SWING_CENTER_DEG + MAX_SWING_OFFSET_DEG
  );

  currentSwing = moveToward(
      currentSwing,
      target,
      SWING_SLEW_RATE_DEG_PER_SEC * dt
  );

  setSwing(currentSwing);
}

void controlledStop(float dt) {
  currentPivot = 0.0f;
  steer(0.0f);
  commandDrive(0.0f, dt);
  commandSwing(SWING_CENTER_DEG, dt);
}

void navigationUpdate(float dt) {
  if (!haveFilteredTarget) {
    controlledStop(dt);
    navState = WAITING_FOR_PI;
    return;
  }

  float distance = filteredDistance;
  float angle = normalizeAngle(filteredAngle);

  if (distance <= HARD_MIN_DISTANCE_FT) {
    emergencyStop(TOO_CLOSE);
    return;
  }

  // Follow-distance hysteresis
  if (!following) {
    if (distance < FOLLOW_START_DISTANCE_FT) {
      navState = IN_LEASH_ZONE;
      controlledStop(dt);
      return;
    }
    following = true;
  } else {
    if (distance <= FOLLOW_STOP_DISTANCE_FT) {
      following = false;
      pivoting = false;
      navState = TARGET_REACHED;
      controlledStop(dt);
      return;
    }
  }

  // Continue an existing pivot until aligned.
  if (pivoting) {
    if (fabsf(angle) <= PIVOT_STOP_ANGLE_DEG) {
      pivoting = false;
      currentPivot = 0.0f;
      steer(0.0f);
    } else {
      navState = PIVOT;
      commandDrive(0.0f, dt);
      commandSwing(SWING_CENTER_DEG, dt);
      currentPivot = calculatePivotCommand(angle);
      steer(currentPivot);
      return;
    }
  }

  // Target behind BB-8.
  if (fabsf(angle) >= REAR_PIVOT_ANGLE_DEG) {
    navState = PIVOT;
    pivoting = true;
    commandDrive(0.0f, dt);
    commandSwing(SWING_CENTER_DEG, dt);
    currentPivot = calculatePivotCommand(angle);
    steer(currentPivot);
    return;
  }

  // Straight.
  if (fabsf(angle) <= ANGLE_DEADBAND_DEG) {
    navState = STRAIGHT;
    currentPivot = 0.0f;
    steer(0.0f);
    commandSwing(SWING_CENTER_DEG, dt);
    commandDrive(calculateDriveSpeed(distance), dt);
    return;
  }

  // Close + significant angle => pivot.
  if (distance <= CLOSE_NAV_DISTANCE_FT &&
      fabsf(angle) >= CLOSE_PIVOT_START_ANGLE_DEG) {
    navState = PIVOT;
    pivoting = true;
    commandDrive(0.0f, dt);
    commandSwing(SWING_CENTER_DEG, dt);
    currentPivot = calculatePivotCommand(angle);
    steer(currentPivot);
    return;
  }

  // Otherwise arc.
  navState = ARC;
  currentPivot = 0.0f;
  steer(0.0f);
  commandSwing(calculateSwingTarget(angle), dt);
  commandDrive(calculateDriveSpeed(distance), dt);
}

// ============================================================
// STATUS
// ============================================================

void sendStatus() {
  Serial1.print("S=");
  Serial1.print(stateName(navState));
  Serial1.print(", Distance=");
  Serial1.print(filteredDistance, 2);
  Serial1.print(", Angle=");
  Serial1.print(filteredAngle, 2);
  Serial1.print(", Drive=");
  //Serial1.print(imuPitch, 2);
  //Serial1.print(", ");
  //Serial1.print(imuRoll, 2);
  //Serial1.print(", ");
  Serial1.print(currentDrive, 3);
  Serial1.print(", Swing=");
  Serial1.print(currentSwing, 1);
  Serial1.print(", Pivot=");
  Serial1.println(currentPivot, 3);

  Serial.print("State=");
  Serial.print(stateName(navState));
  Serial.print(" D=");
  Serial.print(filteredDistance, 1);
  Serial.print(" A=");
  Serial.print(filteredAngle, 1);
  Serial.print(" Pitch=");
  Serial.print(imuPitch, 1);
  Serial.print(" Roll=");
  Serial.print(imuRoll, 1);
  Serial.print(" Drive=");
  Serial.print(currentDrive, 2);
  Serial.print(" Swing=");
  Serial.print(currentSwing, 1);
  Serial.print(" Pivot=");
  Serial.print(currentPivot, 2);
  Serial.print(" HeadFB=");
  Serial.print(headFBCommand, 1);
  Serial.print(" HeadSTS=");
  Serial.println(headSTSCommand, 1);
}

// ============================================================
// SETUP
// ============================================================

void setup() {
  Serial.begin(USB_BAUD);
  Serial1.begin(PI_BAUD);

  pinMode(DRIVE1_PHASE_PIN, OUTPUT);
  pinMode(DRIVE1_PWM_PIN, OUTPUT);
  pinMode(DRIVE2_PHASE_PIN, OUTPUT);
  pinMode(DRIVE2_PWM_PIN, OUTPUT);
  pinMode(PIVOT_PHASE_PIN, OUTPUT);
  pinMode(PIVOT_PWM_PIN, OUTPUT);

  pinMode(RELAY1_PIN, OUTPUT);

  // SAFETY: establish safe outputs before doing anything else.
  digitalWrite(RELAY1_PIN, HIGH);
  analogWrite(DRIVE1_PWM_PIN, 0);
  analogWrite(DRIVE2_PWM_PIN, 0);
  analogWrite(PIVOT_PWM_PIN, 0);

  Wire.begin();

  pca.begin();
  pca.setPWMFreq(50);
  setSwing(SWING_CENTER_DEG);
  centerHead();

  // BNO085 on default I2C address.
  imuOK = bno08x.begin_I2C();
  if (imuOK) {
    Serial.println("BNO085 detected.");
    setReports();
  } else {
    Serial.println("WARNING: BNO085 not detected. Motor control will still run.");
  }

  navState = WAITING_FOR_PI;

  Serial.println("BB-8 Teensy controller ready.");
  Serial.println("Waiting for Pi target packets...");
}

// ============================================================
// LOOP
// ============================================================

void loop() {
  readPiSerial();
  updateIMU();

  uint32_t nowMs = millis();

  // Hardware-level communication watchdog.
  if (systemEnabled &&
      (uint32_t)(nowMs - lastPacketMs) > PI_TIMEOUT_MS) {
    emergencyStop(COMMS_LOST);
    disableSystem();
    resetTargetFilter();
  }

  uint32_t nowUs = micros();

  if ((uint32_t)(nowUs - lastControlUs) >= CONTROL_PERIOD_US) {
    float dt;

    if (lastControlUs == 0) {
      dt = 0.02f;
    } else {
      dt = (nowUs - lastControlUs) / 1000000.0f;
      dt = clampf(dt, 0.001f, 0.10f);
    }

    lastControlUs = nowUs;

    if (systemEnabled) {
      navigationUpdate(dt);
    }

    // Keep the head level from the latest BNO085 pitch/roll reading.
    // This is independent of the navigation state.
    updateHeadLeveling();
  }

  if ((uint32_t)(nowMs - lastStatusMs) >= STATUS_PERIOD_MS) {
    lastStatusMs = nowMs;
    sendStatus();
  }
}

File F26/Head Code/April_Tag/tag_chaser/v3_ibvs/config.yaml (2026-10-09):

pid:
  kp: 15.0
  ki: 0.5
  kd: 2.0

detector:
  nthreads: 2
  quad_decimate: 1.0
  quad_sigma: 0.0
  refine_edges: 1
  decode_sharpening: 0.25

chase:
  stop_distance_cm: 20.0
  steer_limit_deg: 20
  tag_lost_timeout_s: 2.0
  tag_id_chase: 0
  tag_id_world_a: 2
  tag_id_world_b: 3
  world_offset_m: 0.065
  world_offset_tol_m: 0.020
  world_near_zero_tol_m: 0.025
  countdown_s: 3
  world_search_timeout_s: 15
  confidence_threshold: 20.0
  single_tag_world_mode: true   # true = world_a (tag 2) only; skips world_b and pair validation

camera:
  width: 640
  height: 480
  tag_size_m: 0.2
  calibration_file: "../../camera_cal_marker/camera_calibration_pi.yaml"

ibvs:
  kp_pan: 0.05              # deg/px; tune up until oscillation then halve
  kp_tilt: 0.05             # deg/px
  ewma_alpha: 0.8     # smoothing; higher = more responsive, more noisy
  deadband_px: 10           # pixel radius around center where no correction applied
  lazyband_outer_px: 30    # outer edge of soft zone; kp scales 0→full from deadband→this radius (0 = disabled)
  tag_lost_timeout_s: 5.0   # seconds before servos return to neutral after tag0 lost
  tag0_search_hold_s: 0.5  # hold position this long before starting raster search
  ibvs_only: false          # true = run IBVS but skip car centering (Layer 1 tuning)
  tilt_invert: false         # set_cam_tilt_angle(+X) = looks UP on this hardware (confirmed by log analysis)
  log_every_n_frames: 2     # IBVS debug log at ~6Hz (30fps / 5)
  save_frames: false         # set true to save rolling JPEG buffer to session dir (disk-heavy)
  pan_steer_ff_gain:   0.0  # deg pan / deg steer; 0 = disabled. Start at 0, tune to 0.3–0.6
  steer_ff_ewma_alpha: 0.4  # EWMA smoothing for binary steer; lower = slower ramp/decay
  ff_inhibit_px:      15.0  # eu below this px → ff disabled (stuck-car / straight-line protection)
  ff_ramp_px:         20.0  # eu range over which ff scales 0→full above inhibit threshold

world_scan:
  scan_speed_deg_per_frame: 3.0   # degrees moved per camera frame
  pan_range_deg: 60.0             # pan sweeps ±60 degrees
  tilt_levels_deg: [-10, 0, 10]   # tilt positions for raster rows

car_centering:
  kp_car: 0.5                      # steer_deg / pan_deg
  pan_deadband_deg: 8.0            # pan within this range → no steering
  car_centering_speed: 50         # PWM forward speed (0-100)
  tilt_elevation_threshold_deg: 30 # above this tilt, stop driving forward
  decimation_n: 3                  # run car centering every Nth camera frame

servo_limits:
  pan_min_deg:       -90
  pan_max_deg:        90
  tilt_min_deg:      -35
  tilt_max_deg:       35
  steer_min_deg:     -20
  steer_max_deg:      20
  pan_max_delta_deg:   5 # max pan change per frame; caps IBVS step regardless of error
  tilt_max_delta_deg:  5 # max tilt change per frame

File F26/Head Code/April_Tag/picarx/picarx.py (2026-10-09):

from robot_hat import Pin, ADC, PWM, Servo, fileDB
from robot_hat import Grayscale_Module, Ultrasonic, utils
import time
import os


def constrain(x, min_val, max_val):
    '''
    Constrains value to be within a range.
    '''
    return max(min_val, min(max_val, x))

class Picarx(object):
    CONFIG = '/opt/picar-x/picar-x.conf'

    DEFAULT_LINE_REF = [1000, 1000, 1000]
    DEFAULT_CLIFF_REF = [500, 500, 500]

    DIR_MIN = -30
    DIR_MAX = 30
    CAM_PAN_MIN = -90
    CAM_PAN_MAX = 90
    CAM_TILT_MIN = -35
    CAM_TILT_MAX = 65

    PERIOD = 4095
    PRESCALER = 10
    TIMEOUT = 0.02

    # servo_pins: camera_pan_servo, camera_tilt_servo, direction_servo
    # motor_pins: left_swicth, right_swicth, left_pwm, right_pwm
    # grayscale_pins: 3 adc channels
    # ultrasonic_pins: trig, echo2
    # config: path of config file
    def __init__(self, 
                servo_pins:list=['P0', 'P1', 'P2'], 
                motor_pins:list=['D4', 'D5', 'P13', 'P12'],
                grayscale_pins:list=['A0', 'A1', 'A2'],
                ultrasonic_pins:list=['D2','D3'],
                config:str=CONFIG,
                ):

        # reset robot_hat
        utils.reset_mcu()
        time.sleep(0.2)

        # --------- config_flie ---------
        self.config_flie = fileDB(config, 777, os.getlogin())

        # --------- servos init ---------
        self.cam_pan = Servo(servo_pins[0])
        self.cam_tilt = Servo(servo_pins[1])   
        self.dir_servo_pin = Servo(servo_pins[2])
        # get calibration values
        self.dir_cali_val = float(self.config_flie.get("picarx_dir_servo", default_value=0))
        self.cam_pan_cali_val = float(self.config_flie.get("picarx_cam_pan_servo", default_value=0))
        self.cam_tilt_cali_val = float(self.config_flie.get("picarx_cam_tilt_servo", default_value=0))
        # set servos to init angle
        self.dir_servo_pin.angle(self.dir_cali_val)
        self.cam_pan.angle(self.cam_pan_cali_val)
        self.cam_tilt.angle(self.cam_tilt_cali_val)

        # --------- motors init ---------
        self.left_rear_dir_pin = Pin(motor_pins[0])
        self.right_rear_dir_pin = Pin(motor_pins[1])
        self.left_rear_pwm_pin = PWM(motor_pins[2])
        self.right_rear_pwm_pin = PWM(motor_pins[3])
        self.motor_direction_pins = [self.left_rear_dir_pin, self.right_rear_dir_pin]
        self.motor_speed_pins = [self.left_rear_pwm_pin, self.right_rear_pwm_pin]
        # get calibration values
        self.cali_dir_value = self.config_flie.get("picarx_dir_motor", default_value="[1, 1]")
        self.cali_dir_value = [int(i.strip()) for i in self.cali_dir_value.strip().strip("[]").split(",")]
        self.cali_speed_value = [0, 0]
        self.dir_current_angle = 0
        # init pwm
        for pin in self.motor_speed_pins:
            pin.period(self.PERIOD)
            pin.prescaler(self.PRESCALER)

        # --------- grayscale module init ---------
        adc0, adc1, adc2 = [ADC(pin) for pin in grayscale_pins]
        self.grayscale = Grayscale_Module(adc0, adc1, adc2, reference=None)
        # get reference
        self.line_reference = self.config_flie.get("line_reference", default_value=str(self.DEFAULT_LINE_REF))
        self.line_reference = [float(i) for i in self.line_reference.strip().strip('[]').split(',')]
        self.cliff_reference = self.config_flie.get("cliff_reference", default_value=str(self.DEFAULT_CLIFF_REF))
        self.cliff_reference = [float(i) for i in self.cliff_reference.strip().strip('[]').split(',')]
        # transfer reference
        self.grayscale.reference(self.line_reference)

        # --------- ultrasonic init ---------
        trig, echo= ultrasonic_pins
        self.ultrasonic = Ultrasonic(Pin(trig), Pin(echo, mode=Pin.IN, pull=Pin.PULL_DOWN))
        
    def set_motor_speed(self, motor, speed):
        ''' set motor speed
        
        param motor: motor index, 1 means left motor, 2 means right motor
        type motor: int
        param speed: speed
        type speed: int      
        '''
        speed = constrain(speed, -100, 100)
        motor -= 1
        if speed >= 0:
            direction = 1 * self.cali_dir_value[motor]
        elif speed < 0:
            direction = -1 * self.cali_dir_value[motor]
        speed = abs(speed)
        # print(f"direction: {direction}, speed: {speed}")
        if speed != 0:
            speed = int(speed /2 ) + 50
        speed = speed - self.cali_speed_value[motor]
        if direction < 0:
            self.motor_direction_pins[motor].high()
            self.motor_speed_pins[motor].pulse_width_percent(speed)
        else:
            self.motor_direction_pins[motor].low()
            self.motor_speed_pins[motor].pulse_width_percent(speed)

    def motor_speed_calibration(self, value):
        self.cali_speed_value = value
        if value < 0:
            self.cali_speed_value[0] = 0
            self.cali_speed_value[1] = abs(self.cali_speed_value)
        else:
            self.cali_speed_value[0] = abs(self.cali_speed_value)
            self.cali_speed_value[1] = 0

    def motor_direction_calibrate(self, motor, value):
        ''' set motor direction calibration value
        
        param motor: motor index, 1 means left motor, 2 means right motor
        type motor: int
        param value: speed
        type value: int
        '''      
        motor -= 1
        if value == 1:
            self.cali_dir_value[motor] = 1
        elif value == -1:
            self.cali_dir_value[motor] = -1
        self.config_flie.set("picarx_dir_motor", self.cali_dir_value)

    def dir_servo_calibrate(self, value):
        self.dir_cali_val = value
        self.config_flie.set("picarx_dir_servo", "%s"%value)
        self.dir_servo_pin.angle(value)

    def set_dir_servo_angle(self, value):
        self.dir_current_angle = constrain(value, self.DIR_MIN, self.DIR_MAX)
        angle_value  = self.dir_current_angle + self.dir_cali_val
        self.dir_servo_pin.angle(angle_value)

    def cam_pan_servo_calibrate(self, value):
        self.cam_pan_cali_val = value
        self.config_flie.set("picarx_cam_pan_servo", "%s"%value)
        self.cam_pan.angle(value)

    def cam_tilt_servo_calibrate(self, value):
        self.cam_tilt_cali_val = value
        self.config_flie.set("picarx_cam_tilt_servo", "%s"%value)
        self.cam_tilt.angle(value)

    def set_cam_pan_angle(self, value):
        value = constrain(value, self.CAM_PAN_MIN, self.CAM_PAN_MAX)
        self.cam_pan.angle(-1*(value + -1*self.cam_pan_cali_val))

    def set_cam_tilt_angle(self,value):
        value = constrain(value, self.CAM_TILT_MIN, self.CAM_TILT_MAX)
        self.cam_tilt.angle(-1*(value + -1*self.cam_tilt_cali_val))

    def set_power(self, speed):
        self.set_motor_speed(1, speed)
        self.set_motor_speed(2, speed)
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

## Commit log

2026-04-30 Import of all pertinent files from the S26 semester.
    [pid_telemetry1.csv, pid_telemetry10.csv, pid_telemetry11.csv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]
2026-04-30 Folder Reorganizations.
    [pid_telemetry1.csv, pid_telemetry10.csv, pid_telemetry11.csv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]
2026-04-30 Added Electrical Flowchart
2026-05-04 Add guide for files in Body Files directory
    Added a guide explaining the purpose of files in the directory, including Body_Communication, Dead_Reckoning, IMU, Movement_Functions, PID, and PS5_Controller.
